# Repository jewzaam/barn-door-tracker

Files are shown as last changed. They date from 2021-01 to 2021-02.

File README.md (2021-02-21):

When taking pictures of the stars you will get star trails if you don't compensate for the earth's movement.  In some cases this may be a desired shot!  It can be a pretty cool picture.  But for deep sky imaging it's not desired.

I am just getting into astrophotography.  I know it can be expensive to buy gear and I don't know, well, anything yet.  To get started and start learning I made a couple prototype isosoles [barn door trackers](https://en.wikipedia.org/wiki/Barn_door_tracker), one mechanical and one motorized like this, to prove it works.  Then I decided to get more precise and 3D print things.

All docs are in `docs/` and there is an [Index](docs/00-index.md).  My goal is to write up everything you need in order to print, assemble, and use this tracker.  Hope you find some value in this!

Clear Skies!

## Tracker Explained

Posted an 8 min video giving an overview of my setup.

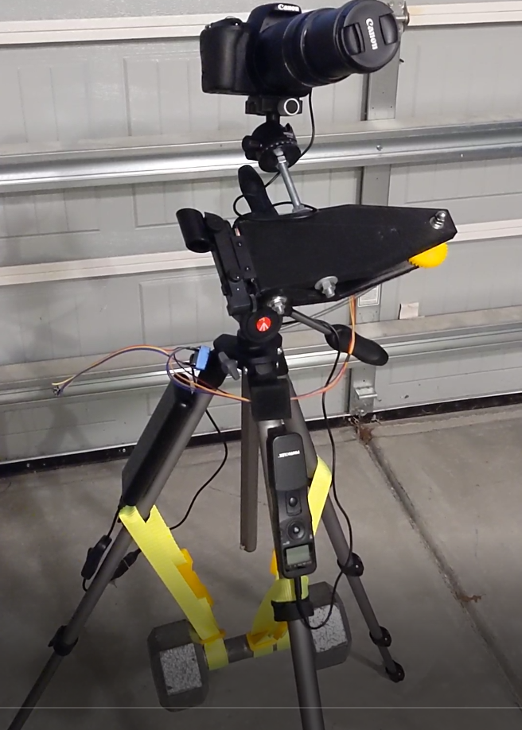
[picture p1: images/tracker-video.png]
Barn Door Tracker Overview (https://youtu.be/gP029RHcJ4Q)


## Tracker in Action
Tracker in Action
All setup and ready to go.  Battery on left leg, intervalometer on right, and 15 lb weight in the backpack.

## [Orion Nebula](https://www.astrobin.com/4iprt9/)<br>
M42
Canon EOS Rebel SL2, 300mm Lens, ISO1600<br>
866 x 5 second lights (1 hr 12 min 7 sec)<br>
[DeepSkyStacker](http://deepskystacker.free.fr/english/index.html) and [GIMP](https://www.gimp.org/).

## [Flame and Horsehead Nebulas](https://www.astrobin.com/a59dnw/)<br>
Flame and Horsehead Nebula
Canon EOS Rebel SL2, 300mm Lens, ISO3200<br>
621 x 5 second lights (50 min 50 sec)<br>
[DeepSkyStacker](http://deepskystacker.free.fr/english/index.html) and [Affinity Photo](https://affinity.serif.com/en-us/photo/).

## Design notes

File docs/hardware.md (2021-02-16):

# Hardware
I staretd out developing this for a Raspberry Pi 4b.  Since I have to the Raspberry Pi Pico for a couple of reasons:

* it's cheaper
* it's easier to smaller
* it starts almost instantly
* it doesn't get as hot

You can still find the older Raspberry Pi 4b [wiring](../imsages/../images/wiring-4b.png) and [software](../src/python/stepper.py), but it is not going to be kept up to date.  At some point I'll likely drop them since the MicroPython code is different enough.

## Raspberry Pi Pico

- File: [main.py](../src/microPython/main.py)
- Config: [stepper.yaml](../src/microPython/stepper.yaml)

The code doesn't hard wire pins but you do have to configure it.  See the [Calibration](#calibration) section on why you don't need to tune the stepper delay.

So just plug in your configuration in [stepper.yaml](../src/microPython/stepper.yaml) and ship the [microPython](../src/microPython/) directory to your Raspberry Pi Pico.

How?  I will leave that to you but provide the tools I used.  I decided to go the VSCode route which is GREAT!  I have one IDE to manage the code, run it remotely on the Pico, and finally to upload it to the Pico.  The sites I found helpful:

- [Raspberry Pi Pico: Getting Started](https://www.raspberrypi.org/documentation/pico/getting-started/)
- [How To Solder Pins to Your Raspberry Pi Pico](https://www.tomshardware.com/how-to/solder-pins-raspberry-pi-pico)
- [Developing for the Raspberry Pi Pico in VS Code — Getting Started](https://medium.com/all-geek-to-me/developing-for-the-raspberry-pi-pico-in-vs-code-getting-started-6dbb3da5ba97)
- [MicroPython libraries](https://docs.micropython.org/en/latest/library/index.html)

Once you get everything uploaded to the Pico it pretty much instantly starts when plugged into USB power.  The Raspberry Pi 4b I used originally took a while.  And it's cheaper, smaller, and MUCH cooler when running.

## Wiring

Pinout picked to minimize wire crossings.  It will change if I start adding some buttons.  Also I used [F-wire-blank.stl](../src/stl/F-wire-blank.stl) to make some blanks for pins not used so I could glue the wires together.  It was super annoying getting to a site to shoot and having to re-wire things!  Thankfully having this repo with pictures made it trivial, but still didn't like it.

The pinout is available on  [Raspberry Pi Pico: Getting Started](https://www.raspberrypi.org/documentation/pico/getting-started/):

Raspberry Pi Pico Pinout

And the layout I have gone with is:

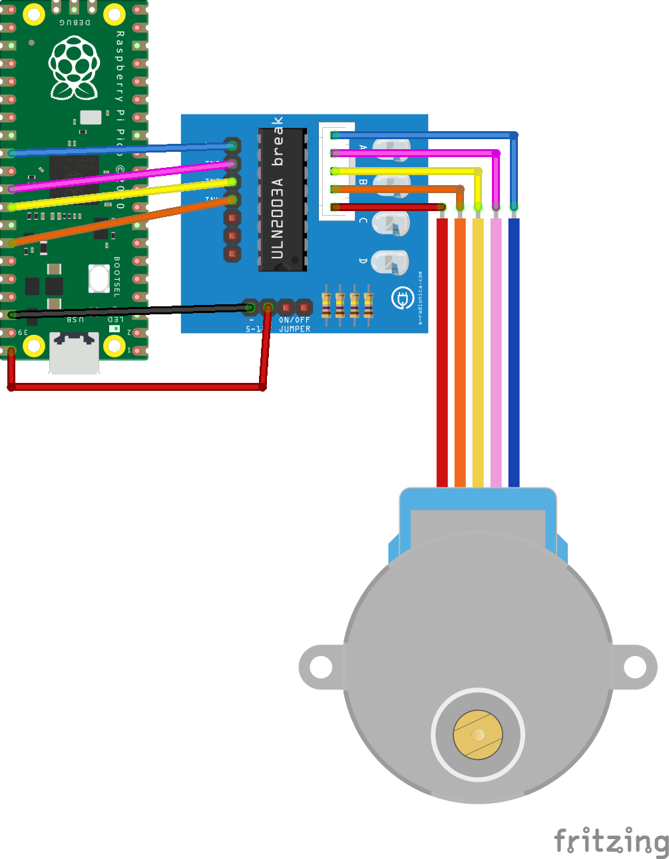
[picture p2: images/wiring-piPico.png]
Raspberry Pi Pico Wiring


## Controls

If you have wired up buttons or a switch (I use a [5-way navigation switch](https://www.adafruit.com/product/504)) you can control the speed of the stepper.  The wiring included is what I used with the switch above so I will talk about it in terms of the directions on that switch: up, down, left, down, and center (press).

When the tracker starts you can have it locked by default.  Control this in [stepper.json](../src/microPython/stepper.json) with `.start_locked`.

- hold control = toggle lock state, hold for `.controls.hold_lock_s` seconds
- up = if unlocked, turn on stepper (forward)
- down = if unlocked, stop stepper
- left = if unlocked, speed up stepper by `.controls.faster_increment`
- right - if unlocked, slow down stepper by `.controls.slower_increment`

Note that faster and slower increments are changes in the configured stepper radius `.tracker.radius`.  The names are not great, sorry.  When you tell this to go faster or slower it is just tweaking the radius and recalculating the step delay.  These values are not written to file.  I had problems getting that to consistently work.

The on-board Pico LED is used to indicate changes...

## Pico LED

The on-board Pico LED (gpio=25) is used to show state and status.

* solid on - tracker controls are unlocked
* solid off - tracker controls are locked
* blinking - various information

The LED blinks briefly when increasing or decreasing stepper speed.

The LED blinks in a pattern to indicate how much adjustment there is from the configured value.  This is shown when the stepper goes from **unlocked** to **locked**.  Initially, the LED turns off.  If the stepper is at the default state it immediately blinks 3 times.  If the stepper is faster it stays off for 2 seconds before blinking.  If the stepper is slower it stays off for 10 seconds before blinking.  If faster or slower, after the delay the LED blinks on once for each step above or below the default speed.  

So if you increased speed 5 times and lock controls the LED will:

1. turn off
2. wait 2 seconds
3. blink 5 times
4. turn off

---
Back to the [Index](00-index.md)!

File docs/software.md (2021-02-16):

# Hardware & Software

I staretd out developing this for a Raspberry Pi 4b.  The code is still there (see [stepper.py](../src/python/stepper.py)) but I have moved on to the Raspberry Pi Pico which is very different.  This document assumes:

- You are using a Raspberry Pi Pico
- You are wiring it the same way documented here
- You can change the code if you use another device or wire it differently

## Accuracy

The current software uses timers for:
* stepper control
* input (irq)
* blinking led

Therefore it is very accurate.  Tuning the radius of the tracker dynamically shows a higher error % on shutdown (print to stdout) but this is momentary in reality because of the use of timers.  Best case is turning on the Pico and no touching any controls until termination.  On termination you get the percentage drift between actual and expected times.  In a 60 second test I got this output:

```shell
avg_actual_delay_ms: 4.94393
total_error_p: -0.01140833%
```

After 4 minutes:

```shell
avg_actual_delay_ms: 4.943915
total_error_p: 0.04760027%
```

After 11 minutes:

```shell
avg_actual_delay_ms: 4.941289
total_error_p: 0.04693866%
```

- `avg_actual_delay_ms` is average delay in ms for each step
- `total_error_p` is the error between actual and expected total times

As you can see, it's pretty close.  It does accumulate some error but it isn't much.  And errors are momentary.  The timer will stive for the configured frequency regardless of what has happened on previous executions.

This is done by having the interupts (timer or irq) set a boolean flag and return.  There's a main control loop that then takes those flags to perform the actions required.  This way the timer blocks as little as possible.  Keep in mind the execution time for a periodic timer (used for stepper control, button input, and led blinking) callback is not part of the timer's period.  Setting 4 coil states took about 250ms.  Having that inside the timer results in a 250ms longer delay than expected.  By moving it out to the main control loop and not part of the timer's interuupt it is executed while the timer is waiting to fire again.

## How Hot Does it Get?

You might worry on a hot summer night about the temperatures.  I was wondering myself!  So I did a very simple test of the temperatures of the Pico, drive controller, and stepper in my office.  They were all resting on my bamboo desk.  The Pico powered by a USB battery (same one I take out for pictures).  The office ambient temperature is 74F.  I am rounding the temperatures as this is only to give peace of mind, not to be a rigerous study of how these components heat up over time.  And the times are simply when I remembered to take the temperatures, not premeditated!

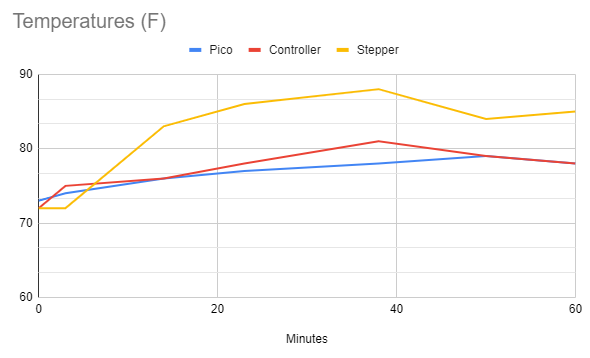
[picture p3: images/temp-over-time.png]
Temperatures over Time


---
Back to the [Index](00-index.md)!

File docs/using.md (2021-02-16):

# Using the Tracker

I am not going into details.  There's enough online on how to use these things.  The basic summary once everything is assembled, code installed, and electronics wired up:

1. Mount tracker on tripod with tracker closed, off, and gears engaged
2. Do polar alignment (use the visual sight if nothing else to get close)
3. Mount camera
4. Turn on tracker
5. Use camera (focus, test shots, exposures etc)

Note I turn on the tracker BEFORE using the camera.  This minimizes star trails from the beginning and makes staying on target easier.  Also, from what I am reading / hearing from folks at 200mm and a comercial low end tracker you'll get 20s to 30s shots.  What you can get depends greatly on polar alignment and correct configuration of the tracker.  Be prepared to try out a lot of things to dial it in!

It's doing its job if you can do a longer exposure with this than untracked.

When done for the night:

1. Turn off tracker
2. Unmount camera and take flats (in whichever order works for you)
4. Setup to take darks
5. While taking darks, take tracker off tripod and cleanup / stow gear

---
Back to the [Index](00-index.md)!

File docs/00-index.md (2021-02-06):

So it's not all in one massive file:

* [Background](background.md)
* [Pricing](pricing.md)
* [Building the Tracker](building.md)
* [Assembly](assembly.md)
* [Hardware](hardware.md)
* [Software](software.md)
* [Using the Tracker](using.md)

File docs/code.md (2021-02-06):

# Code

I staretd out developing this for a Raspberry Pi 4b.  The code is still there (see [stepper.py](../src/python/stepper.py)) but I have moved on to the Raspberry Pi Pico which is a little different.  This document assumes:

- You are using a Raspberry Pi Pico
- You are wiring it the same way documented here
- You can change the code if you use another device or wire it differently

# Raspberry Pi Pico

- File: [main.py](../src/microPython/main.py)
- Config: [stepper.yaml](../src/microPython/stepper.yaml)

The code doesn't hard wire pins but you do have to configure it.  See the [Calibration](#calibration) section on why you don't need to tune the stepper delay.

So just plug in your configuration in [stepper.yaml](../src/microPython/stepper.yaml) and ship the [microPython](../src/microPython/) directory to your Raspberry Pi Pico.

How?  I will leave that to you but provide the tools I used.  I decided to go the VSCode route which is GREAT!  I have one IDE to manage the code, run it remotely on the Pico, and finally to upload it to the Pico.  The sites I found helpful:

- [Raspberry Pi Pico: Getting Started](https://www.raspberrypi.org/documentation/pico/getting-started/)
- [How To Solder Pins to Your Raspberry Pi Pico](https://www.tomshardware.com/how-to/solder-pins-raspberry-pi-pico)
- [Developing for the Raspberry Pi Pico in VS Code — Getting Started](https://medium.com/all-geek-to-me/developing-for-the-raspberry-pi-pico-in-vs-code-getting-started-6dbb3da5ba97)
- [MicroPython libraries](https://docs.micropython.org/en/latest/library/index.html)

Once you get everything uploaded to the Pico it pretty much instantly starts when plugged into USB power.  The Raspberry Pi 4b I used originally took a while.  And it's cheaper, smaller, and MUCH cooler when running.

## Wiring

I chose this layout before physically using it.  It works but there is wire crossover which irks me.  The pinout is available on  [Raspberry Pi Pico: Getting Started](https://www.raspberrypi.org/documentation/pico/getting-started/):

Raspberry Pi Pico Pinout

And the layout I have gone with is:

Raspberry Pi Pico Wiring

## Calibration

You do not have to do calibartion!  This is done automatically.  This section just summarizes the techinque and what to look for in the debug output if interested in how close to expected values things are when you run the code.

This script is simple but not trivial.. it does a dynamic calibration of the delay between steps.  It measure actual time vs expected time and adjusts the delay between steps.  It's done the whole time the program runs.  The key is to do a pretty short sampling.  If you do a long sample it ends up oscillating, swingging wider over time from ideal.  The new step delay is also adjusted to be only 50% of the difference between what would have been ideal and what is currently set.  This simply means a slower change in the delay, again to tamp down on ocillations.  The way it is setup right now works very well to dial in to a reasonable margin of error and keep it there.

Note the error is higher on startup because it is based on the ideal data sheet numbers.  In my testing, _within 10 seconds_ the error rate stars hovering around `0.01%` with a few bips higher but overall very good.

## Custom Sleep

On the Pico I found the sleep functionality to be lacking.  Best I could get was about 1ms granularity.  That's not nearly good enough.  So I wrote a new function, _usleep_, that tries to hit a microsecond target.  It is a busy wait and it's pretty good.  A word of caution on the accuracy (second argument in the function).  If you change the value to be 100% (1.0) you'll be guarneteed to always have longer sleep times than you want.  Why?  Because if the slept time must 100% of the target we'll at best be EXACTLY right.  That never happens.  It will ALWAYS be slightly long.  With a 99% accuracy we allow a little slop and it all averages out pretty well since you'll end up both over andi under.  If you want to tune it I highly recommend you run the code and review the output when the program is terminated.

While on the exit info being printed.. do **NOT** run with `debug = True` when tracking!  This causes a huge load and results in wildly inaccurate sleep times.  Keep the code as lean as possible!

## How Hot Does it Get?

You might worry on a hot summer night about the temperatures.  I was wondering myself!  So I did a very simple test of the temperatures of the Pico, drive controller, and stepper in my office.  They were all resting on my bamboo desk.  The Pico powered by a USB battery (same one I take out for pictures).  The office ambient temperature is 74F.  I am rounding the temperatures as this is only to give peace of mind, not to be a rigerous study of how these components heat up over time.  And the times are simply when I remembered to take the temperatures, not premeditated!

Temperatures over Time
---
Back to the [Index](00-index.md)!

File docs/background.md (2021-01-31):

# Background

## Untracked
When taking pictures of the stars you will get star trails if you don't compensage for the earth's movement.  In some cases this may be a desired shot!  It can be a pretty cool picture.  But for deep sky imaging it's not desired.

For example, here's a 30 second exposure of M42 (Orion Nebula) taken with a 300mm lens.

M42 Untracked 30s

## Manual Tracker 
In order to get better shots of stars (astrophotography) I decided to build a barn door tracker.  My first version was an isometric version, meaning the threaded rod was straight and pivoted to keep in contact with the bottom board as it was rotated.  But it was also manual.  Humans are not good at spinning something consistently at such slow speeds without introducing additional vibrations!

Tracker v1

And it works!  Here's the same shot of M42 but for 150 seconds using the tracker.  It was processed a bit to make the nebula pop out more.  But the point is the lack of star trails.

M42 Manual Tracking 150s

You'll also notice that it isn't super clean.  And my experience doing this wasn't amazing.  Standing still for 2.5 minutes slowly cranking the tracker.. I got distracted, fell behind, added vibrations etc.

## Something Better...

I wanted to get a better shot and not have to manually manipulate this.  After a bit of research I settled on small stepper motor with controller driven by a Raspberry Pi I had laying around.  I have never used a stepper motor so it was a great excuse to learn even more new things.

---
Back to the [Index](00-index.md)!

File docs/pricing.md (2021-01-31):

# Pricing

You may be wondering how much all this will cost you.  I'm breaking down the hardware I used including the estimated plastic by weight from Cura based on my print settings.  For example, I used a small torch to heat the rod for bending on a custom built curved form.  I do include the cost of a Raspberry Pi Pico, though I have not built this with a Pico yet.  I will though so it's a valid cost!

I do **not** include:
- tools
- failed prints
- test prints
- electricity for 3D printer
- cost of items bought in packs larger than what was required
- tripod mounting hardware
- tracker power supply
- and other misc used to build the tracker

This cost is only of parts that end up on your tripod for imaging.

**Grand Total:** $56.08

In the cost breakdown here you can see the _camera mount_ is 53% of the cost.  It's worth it.

## Hardware Store

| Count | What | Cost Each | Total Cost |
| --- | --- | --- | --- |
| 2 | 608-ZZ Bearing | $0.69 | $1.39 |
| 5 | 1/4" Washer | $0.13 | $1.04 |
| 1 | 5/16" x 5" Hex Bolt | $0.64 | $0.64 |
| 1 | 5/16" Hex Nut | $0.13 | $0.13 |
| 1 | 3/8"-16 x 12" Threaded Rod | $1.52 |  $1.52 |
| 3 | 3/8"-16 Hex Nut | $0.14 | $0.42 |
| 2 | 3/8" Washer | $0.15 | $0.30 |
| 1 | 1/4"-20 x 24" Threaded Rod | $1.98 | $1.98 | 
| 3 | 1/4" Hex Nut | $0.08 | $0.24 |
| 2 | 1/4" Lock Washer | $0.19 | $0.38 |
| 2 | 1/4"-20 Cap Nut | $0.25 | $0.49 |
| 2 | #8-32 Bolt | $0.12 | $0.24 |
| 2 | #8 Nut | $0.10 | $0.20 |
| 2 | #8 Washer | $0.08 | $0.16 |
| 2 | M4-0.7 x 8mm Set Screw | $0.37 | $0.74 |

## 3D Prints

Printed parts I calculate based on $23.00 / 1 kg for filament and the settings noted in [Building: Print Settings](building.md#print-settings).

| What | Filament | Cost |
| --- | --- | --- |
| Stepper Gear | 3g | $0.07 |
| Threaded Rod Gear | 17g | $0.39 |
| Tracker Top | 168g | $3.86 |
| Tracker Bottom | 147g | $3.38 |
| Raspberry Pi Pico Case | 6g | $0.14 | 
| ULN2003 Case | 18g | $0.41 |

## Electronics and Camera Mount

And finally other parts.  This includes the camera mount, which is by far the most expensive part.  You don't want your camera to slip though, so it's worth finding something reasonably good.

| What | Cost |
| --- | --- |
| 28BYJ-48 + ULN2003 | $2.48
| Raspberry Pi Pico | $5.00 |
| 6 x F/F Jumper Wire | $0.49 |
| [Tripod Head](https://amazon.com/gp/product/B08FB2Q5RC/) | $29.99 |

---
Back to the [Index](00-index.md)!

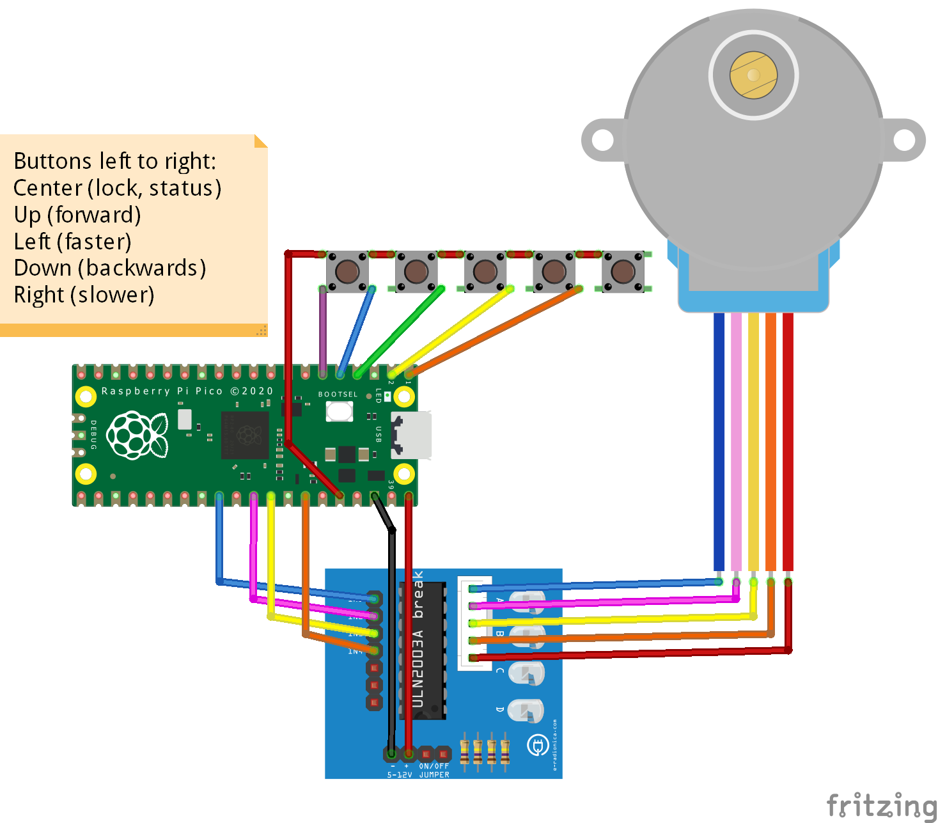
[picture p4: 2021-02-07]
images/piPico+uln2003+28byj-48+5waySwitch.png

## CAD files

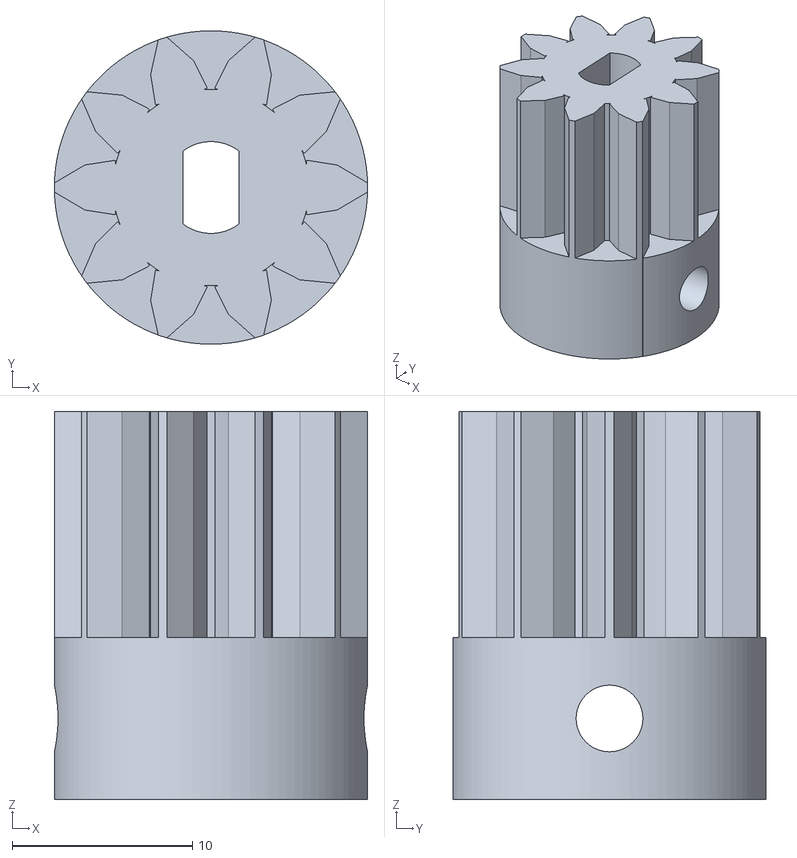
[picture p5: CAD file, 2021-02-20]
src/stl/GEAR-stepper.stl
17.4 x 17.4 x 21.5

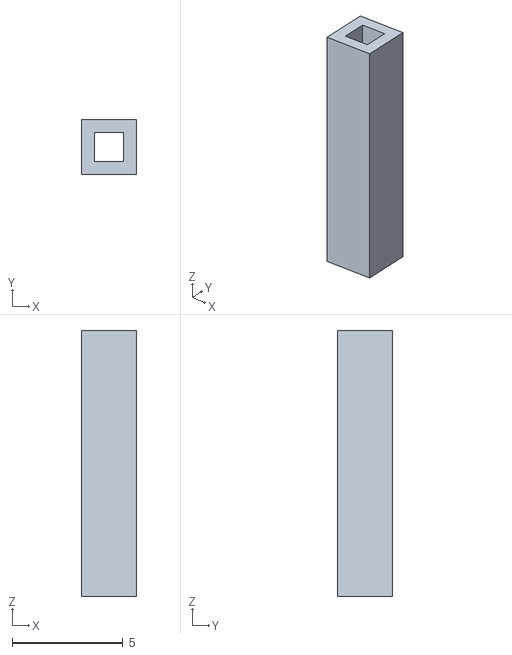
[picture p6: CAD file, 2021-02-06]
src/stl/F-wire-blank.stl
2.50 x 2.50 x 12.0

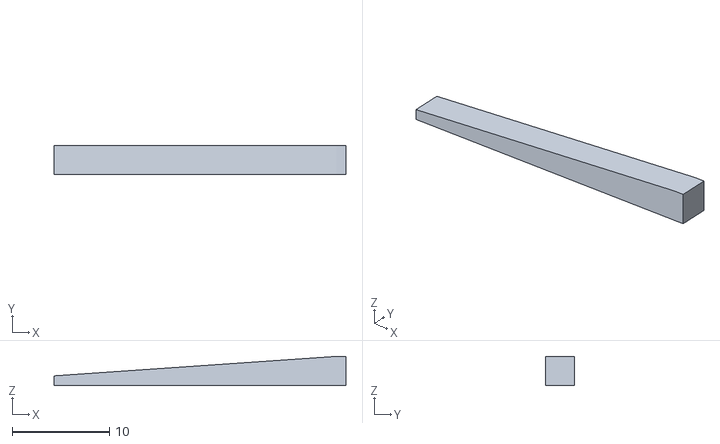
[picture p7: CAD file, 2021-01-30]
src/stl/mini-wedge.stl
30.0 x 3.00 x 3.00

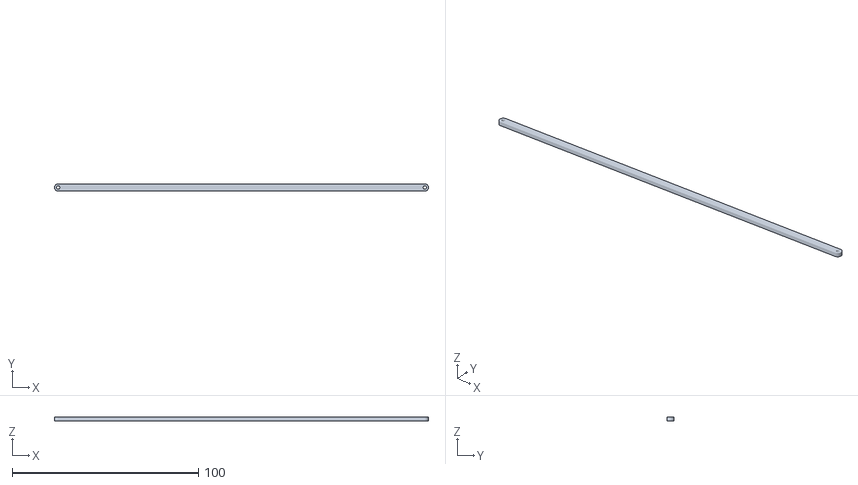
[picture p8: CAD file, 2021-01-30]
src/stl/HELPER-compass.stl
200.8 x 4.00 x 2.00

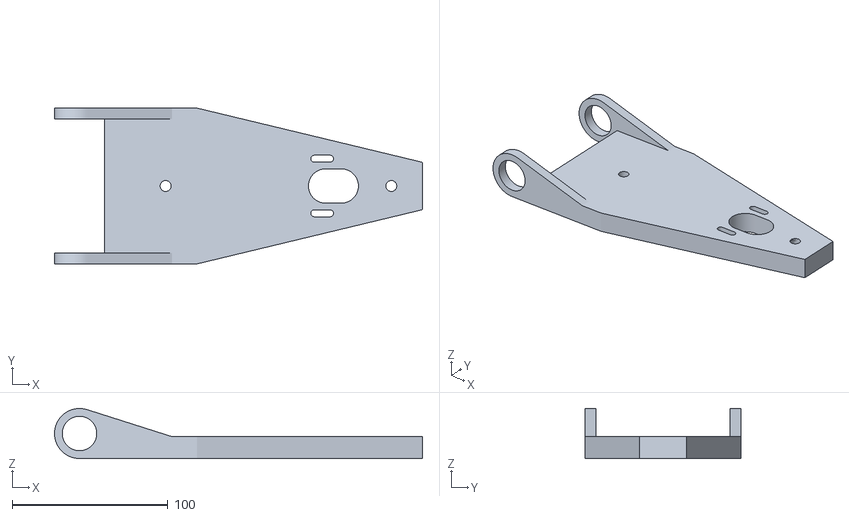
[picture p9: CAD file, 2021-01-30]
src/stl/tracker-bottom.stl
236.1 x 100.0 x 32.1

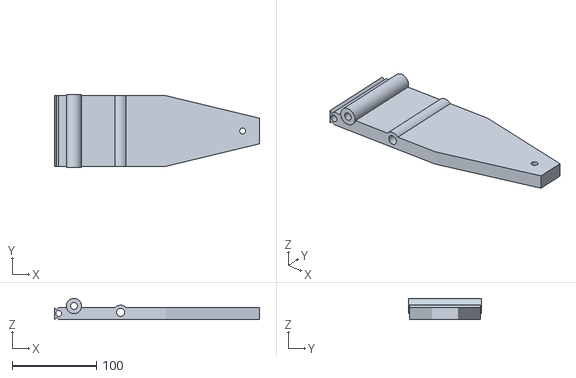
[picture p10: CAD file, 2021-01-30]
src/stl/tracker-top.stl
243.1 x 86.0 x 25.1

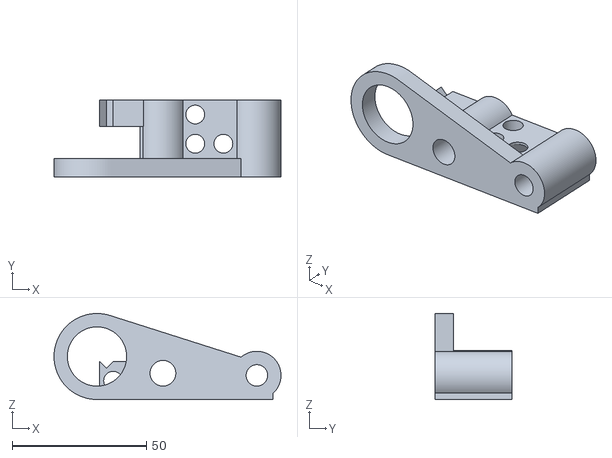
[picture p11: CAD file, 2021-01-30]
src/stl/TEST-hardware.stl
84.7 x 28.8 x 32.1

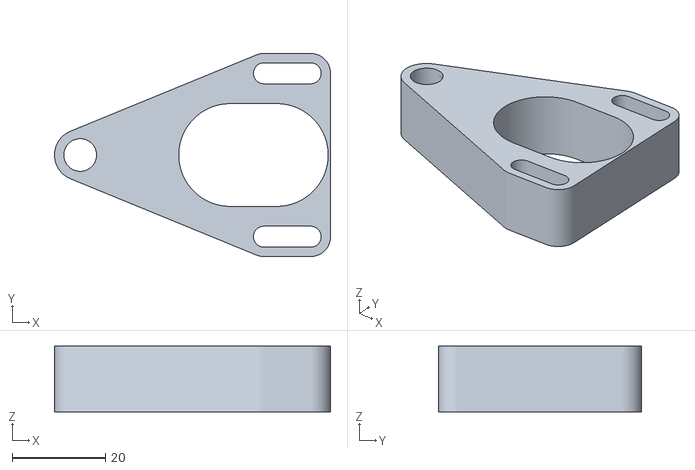
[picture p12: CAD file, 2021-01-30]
src/stl/TEST-gears.stl
59.1 x 43.5 x 14.0

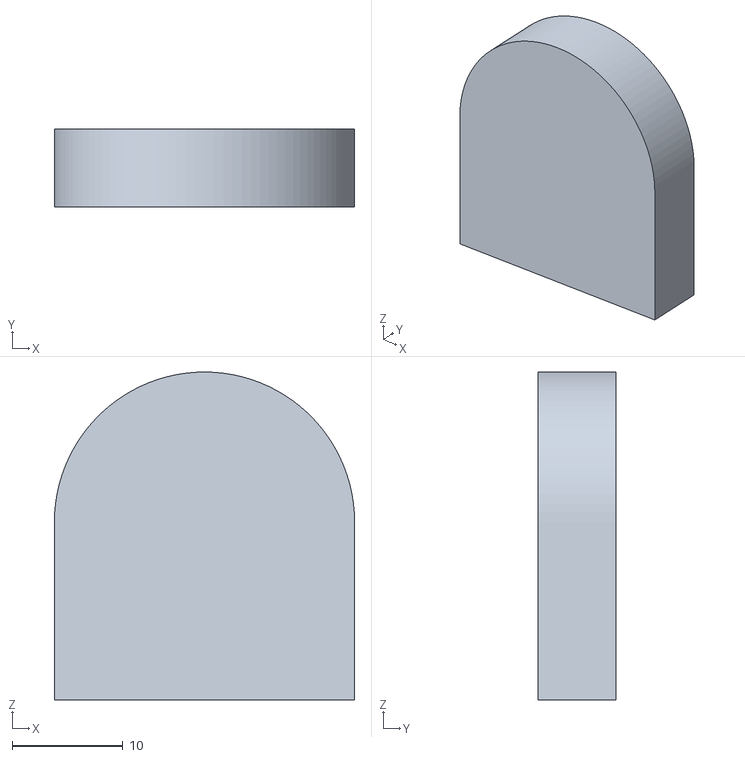
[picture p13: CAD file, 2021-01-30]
src/stl/support-bearing.stl
27.1 x 7.00 x 29.6

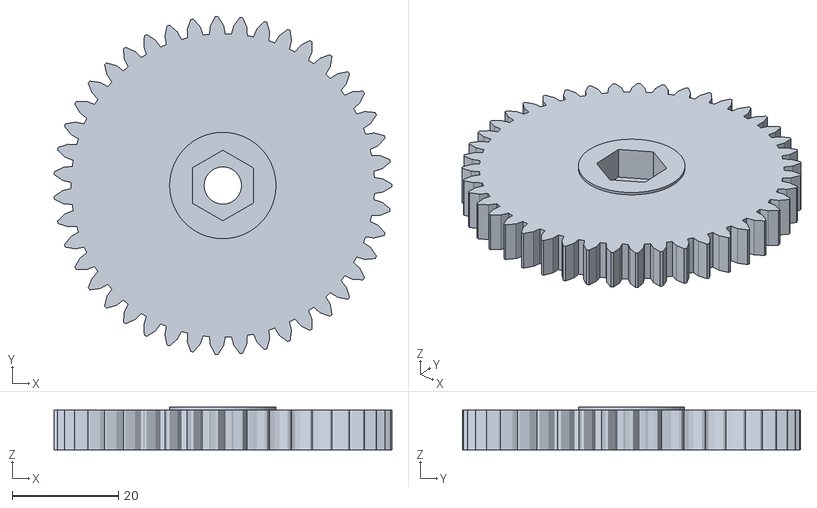
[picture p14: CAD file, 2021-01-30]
src/stl/GEAR-rod.stl
63.6 x 63.6 x 8.00

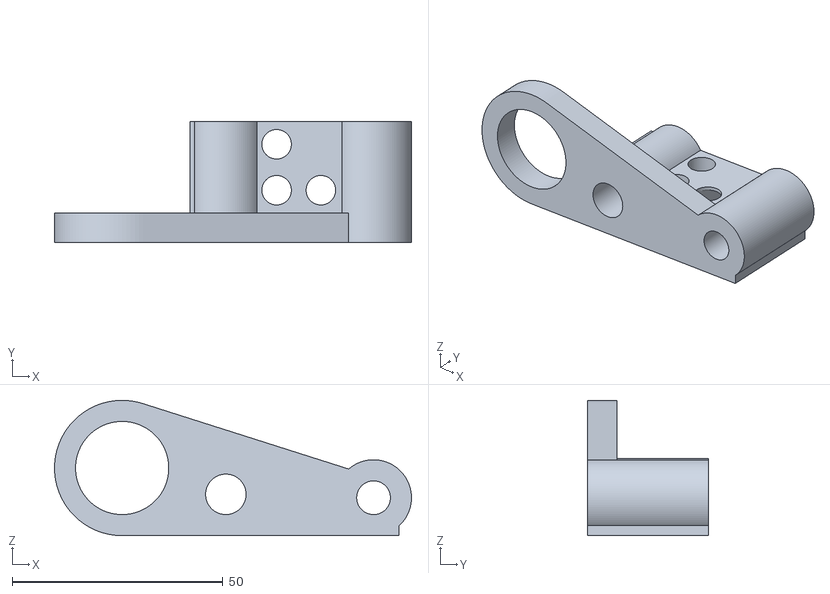
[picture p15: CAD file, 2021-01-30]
src/stl/TESTER-hardware.stl
84.7 x 28.8 x 32.1

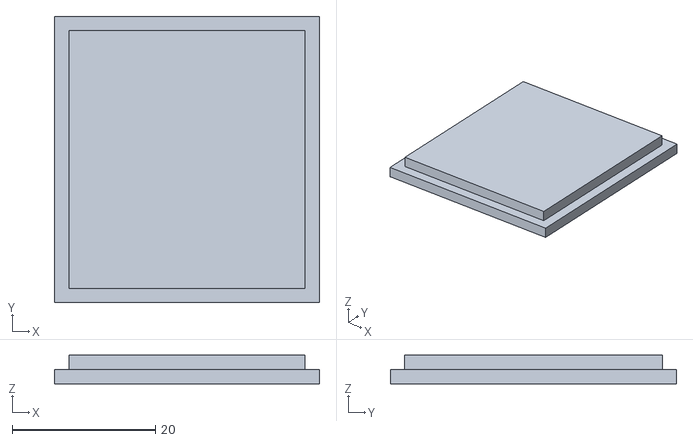
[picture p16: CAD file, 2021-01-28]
src/stl/ULN2003-lid.stl
37.0 x 40.0 x 4.00

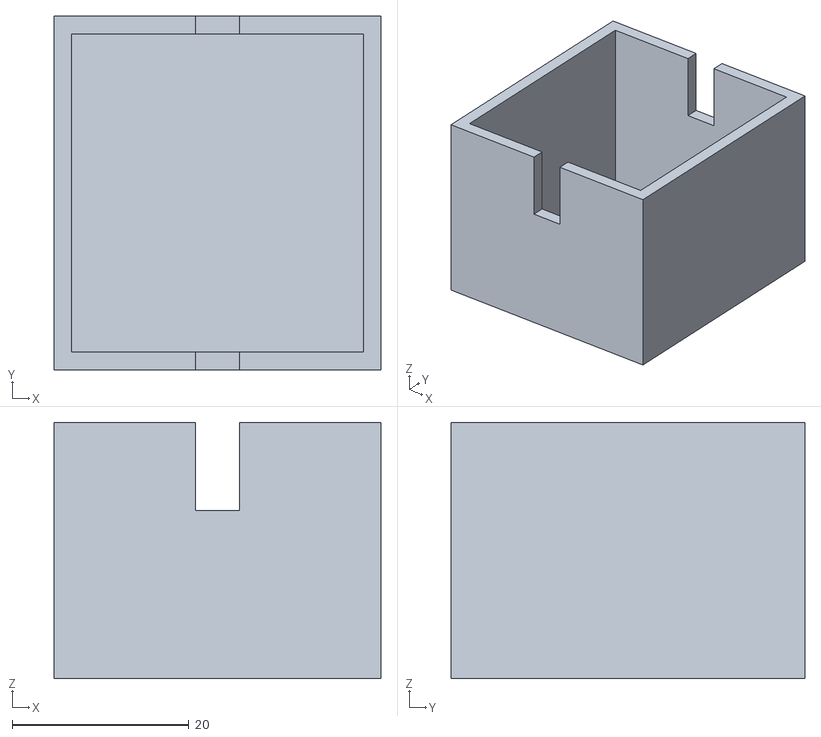
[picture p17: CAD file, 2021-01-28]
src/stl/ULN2003-case.stl
37.0 x 40.0 x 29.0

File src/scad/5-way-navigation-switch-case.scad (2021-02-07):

// quick case and button for 5-way navigation switch
// https://www.adafruit.com/product/504
// adafruit product id 504


switch_hole_d=5.9;


switch_base_xyz=[10.5,10.5,3.7];

case_body_d=20;
case_hole_d=9;
case_body_h=80;

thickness=2;

$fn=200;

/*

Create a case that can be held in hand for use.  The body of the case is a cylinder.  It has a ledge for the switch to sit on and a hole big enough for wiring to fit through.  A lit fits over the switch once it's resting on the ledge
*/

difference()
{
    cylinder(d=case_body_d,h=case_body_h,center=true);
    
cube([switch_base_xyz[0],switch_base_xyz[1],case_body_h+10],center=true);    
}

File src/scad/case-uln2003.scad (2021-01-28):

box_thickness=2;

box_hole_width=5;

box_hole_depth=10;

box_inner_dim=[33,36,25];

/* [Hidden] */

$fn = 300;


module lid()
{
    // lid
    union()
    {
        cube([box_inner_dim[0]+box_thickness*2,box_inner_dim[1]+box_thickness*2,box_thickness]);

        translate([box_thickness,box_thickness,0])
        cube([box_inner_dim[0],box_inner_dim[1],box_thickness*2]);
    }
}

// box
module box()
{
    difference()
    {
        // main body
        cube(box_inner_dim+[box_thickness*2,box_thickness*2,box_thickness*2]);

        // cut inside
        translate([box_thickness,box_thickness,box_thickness])
        cube(box_inner_dim+[0,0,box_thickness*2]);
        
        // cut slot for wires
        translate([box_thickness+box_inner_dim[0]/2-box_hole_width/2,-box_thickness,box_thickness*2+box_inner_dim[2]-box_hole_depth])
        cube([box_hole_width,box_inner_dim[1]+box_thickness*4,box_hole_depth+box_thickness]);
    }
    
}

lid();

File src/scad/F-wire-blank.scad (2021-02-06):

xyz=[2.5,2.5,12];
thickness=0.6;

difference()
{
    cube(xyz,center=true);
    cube(xyz+[-thickness*2,-thickness*2,thickness*2],center=true);
}

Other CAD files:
src/stl/gear-10.stl
src/scad/mini-wedge.scad
src/scad/tracker.scad

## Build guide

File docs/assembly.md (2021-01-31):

# Assembly

Follow the sub-sections in order...

## Prep: Sanding / Filing

1. Make sure the bottom plate is smooth where the 43 tooth gear will rest.
1. Make sure the bottom plate's rod hole is smooth but don't make it too wide!
1. Cleanup the bottom plate bearing support.  Don't get it so the bearing can be hand pressed in, you can do that with the bolt and a few larger washers.  Cleanup both sides EVENLY if possible!
1. Cleanup teeth on all gears.  Do not take off much material but make sure there are no odd protrusions that will cause gears to push each other and move the tracker.
1. Cleanup the inside of the stepper gear so it fits on the stepper motor.
1. Generally cleanup anything else.. 

## Bearings

Gently press the bearings into the bottom plate.  Be sure to put the pressure on the outer bearing race, not the inner, else you may damage the bearing.  It shouldn't be too hard to press it in, so if it's really hard cleanup some with a file or sandpaper.

To press them in stach washers such that the biggest washer is on the outer race and the hinge bolt won't slip through it.  Use washers on both sides.  Gently screw the bolt onto the bearing with the nut you have for the hinge.  

Remove bolt and repeat for the other bearing.

Here are some example pictures of me testing this process on the hardware test print.  Note this doesn't have the simple finder test print.  Flip the bolt around the other direction if that bumps into the bolt.

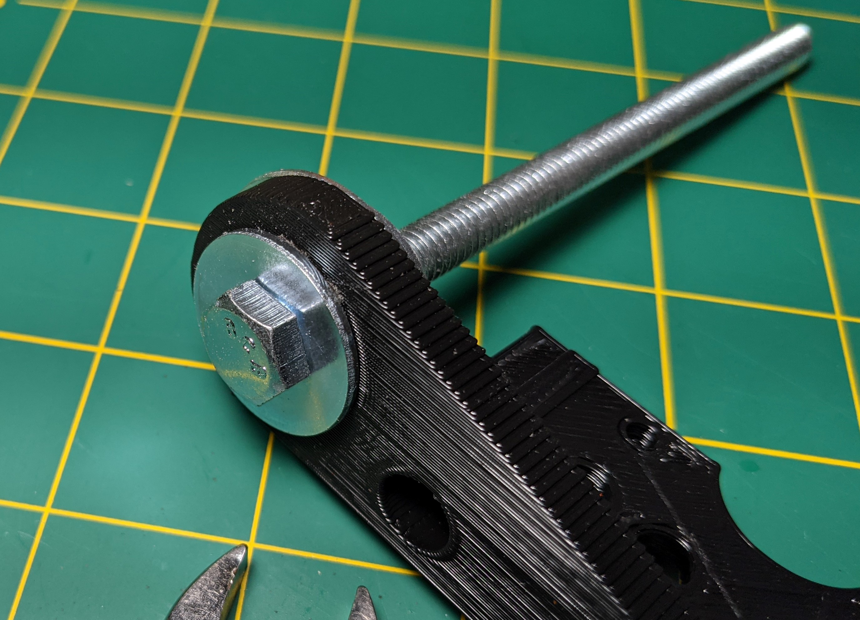
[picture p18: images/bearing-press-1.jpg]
Bearing Press 1

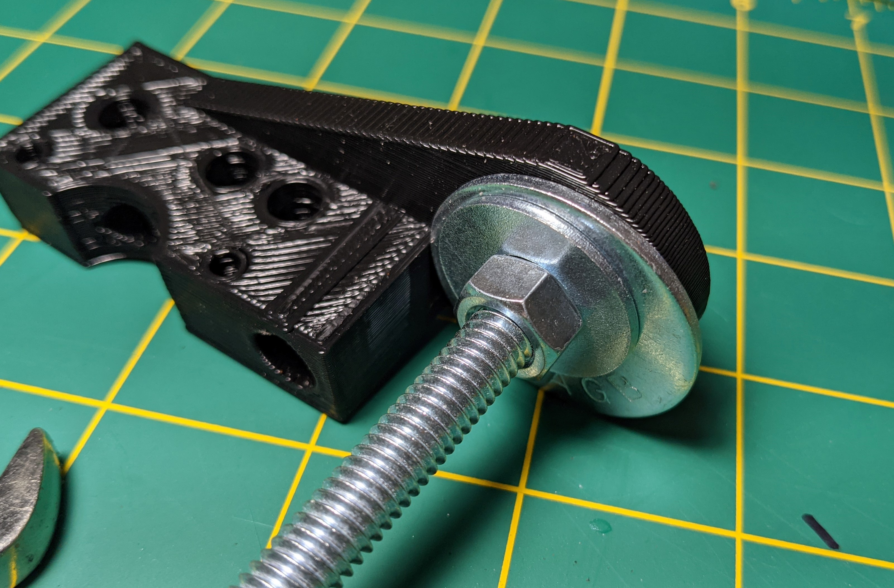
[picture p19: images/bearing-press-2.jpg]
Bearing Press 2

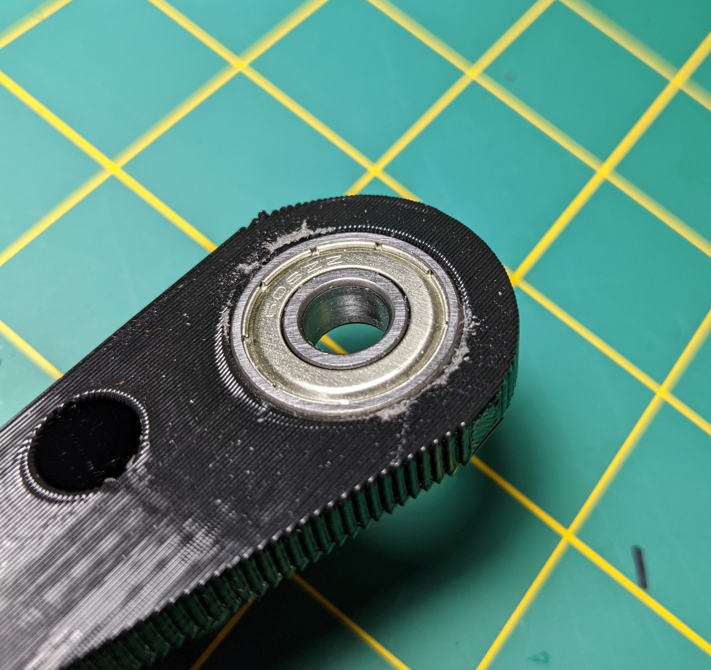
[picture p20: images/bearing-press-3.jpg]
Bearing Press 3


## Hinge Bolt

Make sure you get the right orientation for the plates.  When closed, the sides that were on your print bed are on the outside!

Note I am adding some 1/4" washers to ensure the bolt and nut have a solid and flat surface on the outside of the bearing.  This is not required.

Then...
1. Place the top plate in between the bearings in the correct orientation. 
1. Place one 1/4" washer on the 5/16" hex head bolt.
1. Thread 5/16" hex head bolt through one bearing.
1. Push or thread bolt through the top plate.
1. Add one 1/4" washer on the bolt.
1. Gently tighten.  This may mean tightening the bolt head if threaded through the top plate AND tightening the 5/16" nut.
1. Check alignment of the threaded rod holes between top and bottom.

### Troubleshoot

If the rod holes do not align it's probably due to over extrusion and filing away material inconsistently between the two bearing holes.  Mine was off by at least 1mm resulting in a huge misalignment at the end of the tracker.

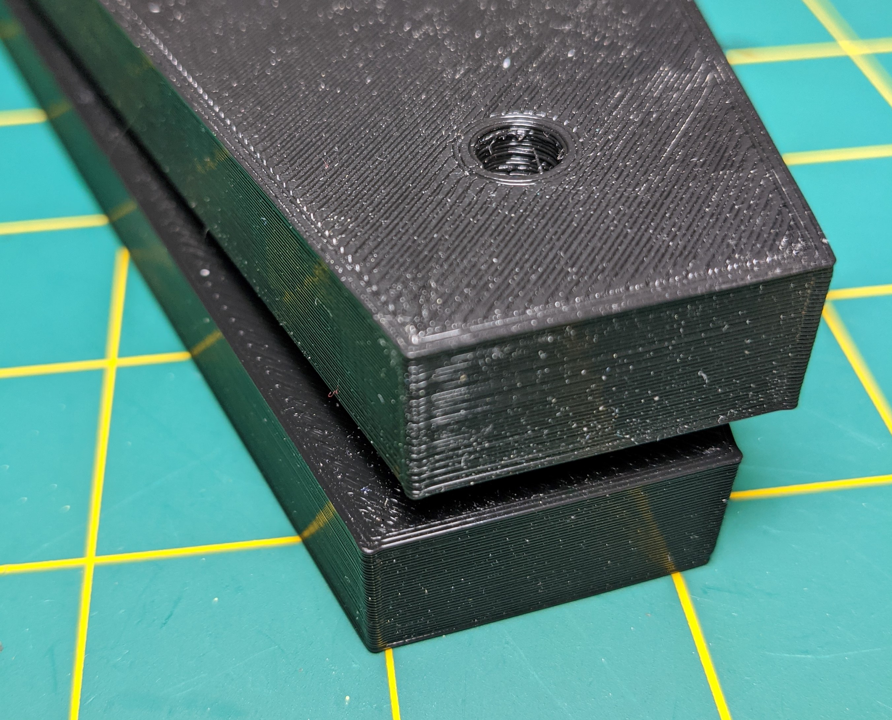
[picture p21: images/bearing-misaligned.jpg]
Bearing Misaligned


I don't know what I did wrong but whatever.  Going to make it work!  My solution was to find which hole needed adjustment and slowly sanding with 80 grit sandpaper on a dowel.  The side effect of this was a gap on the back side of one bearing.

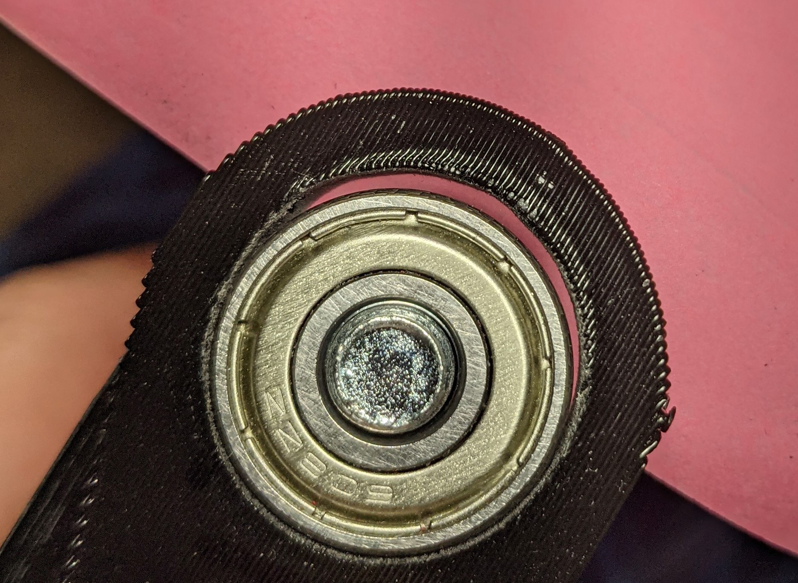
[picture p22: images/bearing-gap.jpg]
Bearing Gap


Create and print the [mini-wedge.stl](../src/stl/mini-wedge.stl) and if needed adjust with the [mini-wedge.scad](../src/scad/mini-wedge.scad).  Put in wedges as needed, glue in, and cut flush.  Do this after sanding and with your straight (not yet curved I assume) threaded rod inserted into both the top and bottom plates.  The closer you get this to perfect the better!  Which is why I'm bummed I had to write this section.  But it is what it is!

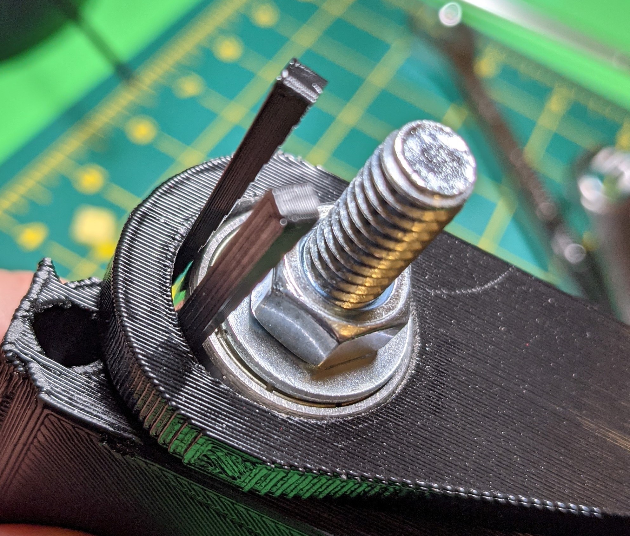
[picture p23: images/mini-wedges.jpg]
Mini Wedges


## Stepper Gear

You may have to push the 10 tooth gear onto the stepper motor.  But if you have to push really hard STOP.  Take the time to file down the inside.  You'll need some small hobby files, but if you have a 3D printer you should get some anyway.  Once it fits down snug but not too snug thread the #6 set screw into one side of the gear.  Optionally use a second #6 set screw.

**NOTE** take care to note if the stepper gear is tilted.  This is easier to do powered, since you can simply eyeball a full rotation and see if it seems the teeth wobble over the course of a rotation.

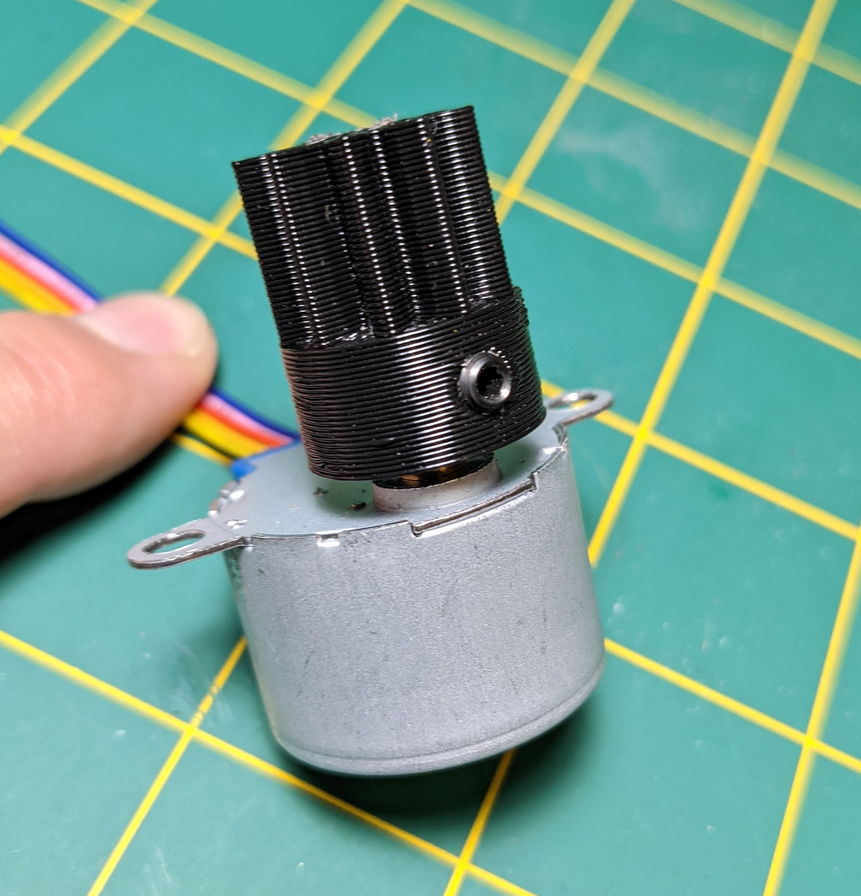
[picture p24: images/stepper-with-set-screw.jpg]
Stepper and Gear with Set Screw


## Stepper (with Gear)

Thread 2 #8-32 x 1" machine screws through the motor mounts into the 2 holes on the bottom plate.  Of course the gear must go UP into the bottom plate, so you can't get the orientation wrong unless you try really **really** hard..

Slide stepper as close to hinge as possible and **loosely** tighten bolts with #8-32 nuts, optional washers.  We will adjust the stepper location in a later step, but it's much easier to install before the threaded rod is on the tracker.

## Threaded Rod and Gear

For now just a quick summary.  More info to come..
1. Bend the rod.
1. Open tracker.
1. Secure to top with washers, lock washers, and nuts (1 ea top and bottom).
1. Install 43 tooth gear (with nuts).
1. Thread end of curved rod into bottom plate.
1. If necessary, bend AT THE TOP PLATE to get it to fit in the bottom plate.  Do not remove any curve!
1. Thread 1/4" cap nut on end of the curved rod.

**NOTE** Once you install this on a tripod you may find it is too long, interfering with tripod legs.  You'll get hours of time out of this even shortening it a lot.  Feel free to cut short with a hack saw, smooth out the threads, and put the nut cap back on.

## Adjust Stepper

With the threaded rod gear near the end of the curved rod..

Loosen the stepper bolts and slide it so that the stepper gear is interacting with the threaded rod gear where you want.  This may take some tuning to make sure it's not too loose or tight a fit.

**NOTE** imperfections in the gears may cause things to move around while taking shots.  If you notice things binding see if you can smooth any of the gears or adjust the distance between the stepper and threaded rod gears.

## Camera Bolt

Thread or push your 3/8" bolt through the camera bolt hole.  Tighten as needed.  Attach camera mount on the polar said of the tracker.

If this bolt is very long the whole thing will bounce more.  Using a 3/8" threaded rod for this allows you to adjust the length by changing how long the rod is on the camera (polar) side.

1. install one washer and nut
2. insert rod into camera hole
3. install other washer and nut
4. adjust location based on where you think you want the camera mount
5. tighten
6. thread one more nut
7. install camera mount
8. lock camera mount by tightening last nut on the base of the camera mount

Be careful not to tighten the nut too much on the camera mount.  Unless you got a really nice one (you didn't did you..) you could break the threads off of the mount.

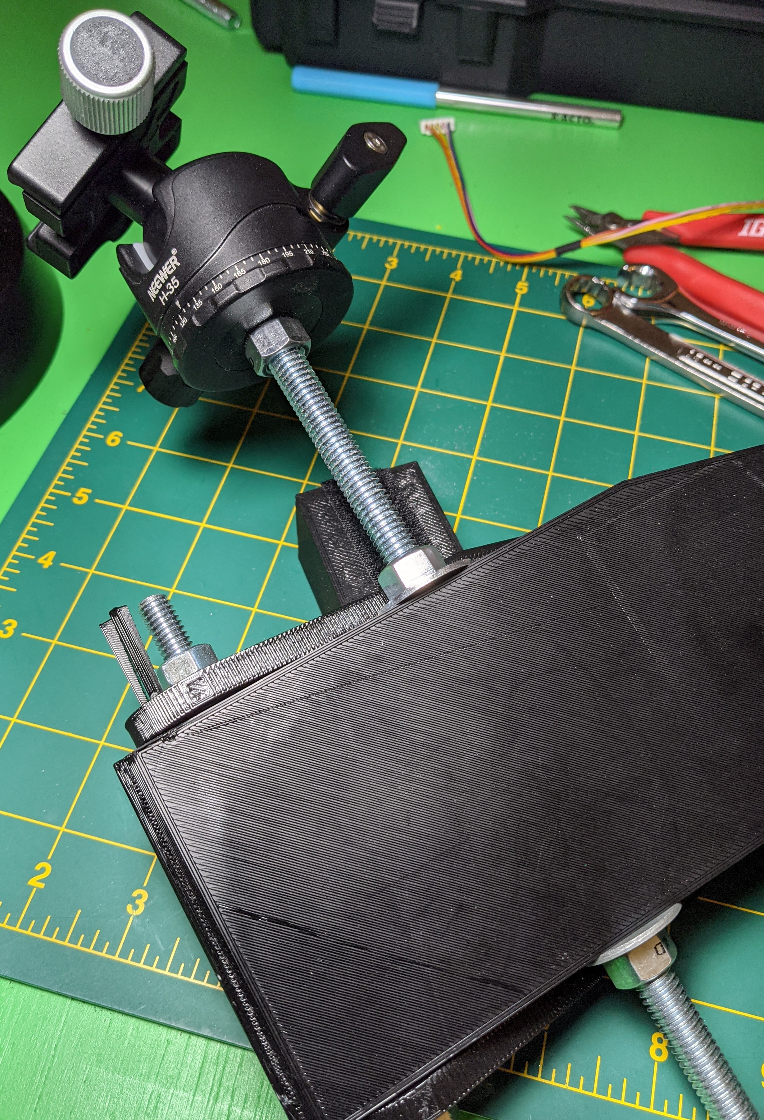
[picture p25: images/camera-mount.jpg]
Camera Mount


## Tripod Bolt

This is specific to your tripod.  You may need to replace the bolt you have on the tripod with something longer.  Whatever you have, thread it through the bottom plate hole and secure with a nut.  Consider a T-nut and a shorter bolt if you don't want it protruding.  The T-nut requires a wider hole and could be pressed in after heating (so the tines will melt the plastic when being pushed).

Note my bolt is too long and I plan to cut it short and heat a T-nut to secure it.  Just do what is right for your setup..

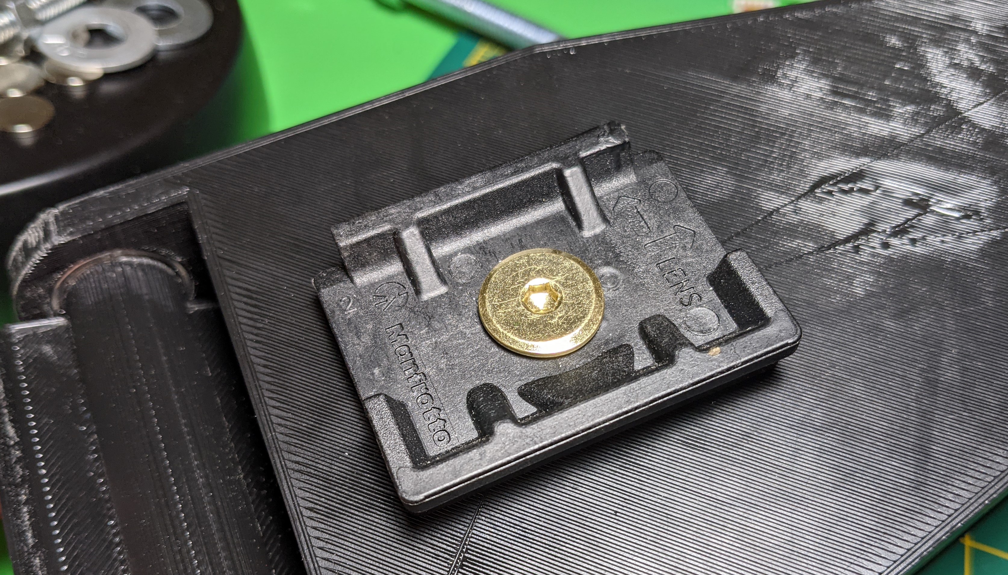
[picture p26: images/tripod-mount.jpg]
Tripod Mount


## Other Electronics

The drive controller and Raspberry Pi installation I leave to you.  Just make sure:
1. lights on these will not interfer with your pictures
1. the threaded rod will not hit them
1. they are in a good location when the tracker is both fully closed AND fully open

---
Back to the [Index](00-index.md)!

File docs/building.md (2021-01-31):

# Building the Tracker

NOTE I am not affiliated with Amazon.  Any links I provide are just to help you out by providing exmaple hardware!

## How does it work?

The first thing is to understand how the stepper works.  Actually, the first thing is to decide what stepper to use.  I selected the 28BYJ-48 stepper motor with ULN2003 driver board.  Once the parts arrived I dove in trying to understand how it works.

There are tutorials and data sheets. And they are almost right.  But they ultimately don't quite get you there.  Here are a few I was referencing:

* [28BYJ-48 Data Sheet](https://components101.com/motors/28byj-48-stepper-motor)
* [Raspberry Pi Stepper Motor Control with L293D / ULN2003A](https://tutorials-raspberrypi.com/how-to-control-a-stepper-motor-with-raspberry-pi-and-l293d-uln2003a/)
* [Adafruit's Raspberry Pi Lesson 10. Stepper Motors](https://learn.adafruit.com/adafruits-raspberry-pi-lesson-10-stepper-motors/overview)

What these give you is parts of the info but not everything.  And for reasons I cannot fathom the Raspberry Pi tutorial does not plug the stepper straight into the drive board!  I tinkered around and firgured out how to do it and here's the key things I learned.  Please keep in mind I haven't touched a Raspberry Pi since I setup OctoPi for my 3D printer 5 years ago, so I know almost literally nothing..

This model of stepper motor has 5 wires.  The colors are important, NOT the order they may be in the wiring harness.  Red is power, the others correspond to a coil by color.  There are 4 coils.  To move the motor you turn the coils on in a specific pattern.  There are several possible patterns but the recommended pattern uses 1/2 steps for this stepper.  Do that.  It's more steps in a sequence but you're writing code.  If it's just slightly more complex and RECOMMENDED who cares?

The wires from the stepper are connected on the side of the driver board with a clip for the stepper.  On the other side you hook up GPIO from the Pi.  The GPIO will will turn the coil ON.  This is important to note, as the data sheet indicates the sequence by which coil is held to ground and is therefore on.  So "0" on the data sheet is "1" in your program.

And don't forget power!  You can turn on the coil GPIO all you want, but without power turned on it does nothing.  Well, it still may do nothing if you wire it wrong, but that's a different problem!

Finally the question of speed.  This is controlled only by the delay between steps.  There's a HUGE gotya on this one:  each step will take a different amount of time.  Meaning it is not an accurate system.  But we can compensate for that.

Now for some math.  We are driving some gears that push a threaded rod.  We need to know how fast that rod will move.  The stepper has a motor in it and the data sheet gives how many degrees it moves per step. BUT it also has a gear reduction inside the motor.  So the stepper shaft moves on rotation based on that reduction.  The 28BYJ-48 stride angle is listed as "5.625°/64".  This means each step is 5.625° and the gear reduction is 64:1.  So one rotation is (360/5.625*64) = 4096 steps (using the recommended half step sequence).  This means to get our gears to turn at a specific rate we can simply put the right delay between steps.  But not really.  As noted, it isn't accurate.

To compensate for timing inacuraces in either the Pi or in the stepper I spent a good bit of time trying out things.  It's very easy to get a system setup that oscillates and gets worse over time.  The best pattern I found was to do a short snapshot of the expected vs actual time observed over a known number of steps and adjust the delay based on what was observed.  It won't be 100% accurate but we're talking 100's of ms over the course of half an hour, something like 0.025% drift.  Unless you're taking 30 minute exposures you won't notice it!  By the way, you won't take 30 minute exposures.  At 300mm I probably will try only 30 seconds. But that's better than the 2 seconds untracked by a LOT!

We have a stepper, and it's pretty accurate.  We just need to know what gears we're turning and the rod it's pushing so we know the delay for the stepper and the distance to put the rod from the pivot.  This model will let you pick these values if you have something different to work with.  

Key values to know:
* how many threads per mm for your rod
* how far center of rod is from the pivot point

I went with things from other models I saw around the interwebs and what I could get in my local hardware store:

* 1/4 inch threaded rod, 20 threads per inch
* rod 200mm from the hinge, because of print bed size

The radius (r) is 200mm.. And there are 0.7874 threads per mm (aka 20 threads per inch).  The circumference of the circle your rod travels is 2πr = 400π = 1256.6370mm.

The earth roughly rotates 360° / 24 hours, or 0.25° / minute.  Put another way, every minute the earth rotates 1 / 1440 % of the circumference of your circle.  That means every minute the rod needs to travel 0.8726mm.  (**NOTE** it isn't exactly / 24 hours, we will use the real value in the stepper code)

What we really need is the how many revolutions a nut on the rod must turn per minute.  Why the nut?  Our gear drives a nut, and one rotation is the distance of one thread along the rod.  And we pick one minute simply as a reasonable time scale to work with.  The rotation speed must be enough to move the rod 0.8726mm a minute.  Given 0.7874mm per thread that works out to 1.1082 rotations in a minute.

Now let's put that all together.  Our input date is:
- rod has 20 threads per inch (20 thread / 24.5 mm)
- radius of circle is 200 mm

Therefore we calculate the rotation required of the nut on the threaded rod per minute is:

(400π/1440) / (20/25.4) = 1.1082 revolutions per minute

Many barn door trackers work on a 1/4" rod at 290mm radius, which works out to 1 rotation per minute.  My motorized prototype did this just fine and the stepper could go faster.  This is a very doable number!  Let's get into building...

## Parts

Ok, explainations..

The tracker opens slowly on a hinge.  It's driven by your gears moving the threaded rod.  There are bearings at the hinge to help it be very smooth and the bolt just holds the bearings in the right place.  You attach the tracker to a tripod.  This should be sturdy.  Many tripods in the US have 3/8" bolts.  Mine has a 1/4" bolt.  You attach the camera on a separate camera mount.  I recommend a ball mount as the adjustment screws will not get in the way.  Again, in the US it's either 3/8" or 1/4".  Use the biggest you can for stability!

A note on camera mounting.  This model mounts it on the side of the tracker.  This provides more flexibility for getting shots.  If you mount it on the top it's likely you'll be limited since the ball mount won't allow enough movement to point at zenith.  I don't provide an option for a top mount because of this limitation.

If you are not using a 28BYJ-48 stepper motor you'll need ot adjust other parameters.  I won't get into these here.  And they're likely to be hard coded in the initial model anyway.  Sorry about that!

Buy the hardware first so you can measure things!

Make sure your hinge bolt is long enough.  You want the tracker to be around 4 inches (~100mm) wide.  If it's too long it's easy to cut it shorter with a hack saw.  It's really hard to make it longer..

If you don't have mini files yet do yourself a favor and get some.  They make cleanup much easier.  And if you get a set without handles just print some and heat press the file into the plastic!  I have a set similar to this [carbon steel 6 piece-set](https://amazon.com/dp/B07KH8BG1F/).

Hardware I used that is default for the model:
- Hinge
  - 2 ea: 608-ZZ bearings
  - 1 ea: 5/16" x 5" hex full thread bolt
  - 2 ea: 1/4" washer
  - 1 ea: 5/16" nut
- Camera Mount
  - 1 ea: 3/8" threaded rod
  - 2 ea: 3/8" washer
  - 3 ea: 3/8" nut
  - 1 ea: ball head tripod mount
- Threaded Rod
  - 1 ea: 1/4"-20 x 20" threaded rod (20 thread / inch)
  - 2 ea: 1/4"-20 nut
  - 2 ea: 1/4" washer
  - 1 ea: 1/4" washer (optional, under gear
  - 2 ea: 1/4" lock washer (optional)
  - 2 ea: 1/4"-20 cap nut (optional)
- Threaded Rod Gear
  - 1 ea: 1/4"-20 nut
- Stepper
  - 2 ea: #8 x 1" bolt
  - 2 ea: #8 washer
  - 2 ea: #8 nut
  - 1 ea: 28BYJ-48 stepper motor
  - 1 ea: ULN2003 driver board
  - 1 ea: Raspberry Pi of your choice
  - 6 ea: F/F jumper wire
  - 1 ea: 5V power supply for Raspberry Pi
- Stepper Gear
  - 1 ea: M4-0.7 x 8mm set screw

3D printed part list:
- 1 ea: 10 tooth stepper gear
- 1 ea: 43 tooth rod gear
- 1 ea: tracker top and bottom
- 1 ea: ULN2003 case and lid
- 1 ea: Raspberry Pi cases

Also included are 3D prints to test hardware and gears.  Use them!

### TEST models

- File: [tracker.scad](../src/scad/tracker.scad)
- Parts: **TEST: Hardware**, **TEST: Gears**
- STL: [TEST-hardware.stl](../src/stl/TEST-hardware.stl), [TEST-gears.stl](../src/stl/TEST-gears.stl)

This contains two test.  One is a block that you can test the bearing and **all** threaded hardware.  The other you verify placement of gears.  The gear placement model is techincally optional but I liked testing the gears on a quick print (30 minutes) before firing up the full tracker print (15 housr).

Please use these before you print the full model!  This will let you know if you need to tune any parameters for final print, including gear placement.

The "TEST: Hardware" model is very busy.  What you're testing and the params to tweak:
- Bearing = try pressing your bearing into the model.  It's better to break the test than the real model!
    - `bearing_diameter`
    - `bearing_height`
- EZ-Finder Mount = if you have a finder, see if it fits on here
    - nothing to tweak, it's hard coded.. you can glue something to the flat surface
- Visual Finder = just for reference, you don't do anything with this but look through without aid
    - nothing to tweak
- Camera Bolt = test your camera bolt goes into this as desired
    - `camera_bolt_diameter`
- Tripod = verify tripod bolt fits
    - `tripod_bolt_diameter`
- Hinge Bolt = test the hinge bolt
    - `hinge_bolt_diameter`
- Rod, Top = make sure the rod fits as desired
    - `rod_diameter`
- Rod, Bottom = the curve should be OK for the model, but you can verify with this
    - `rod_diameter`
    - `rod_T`

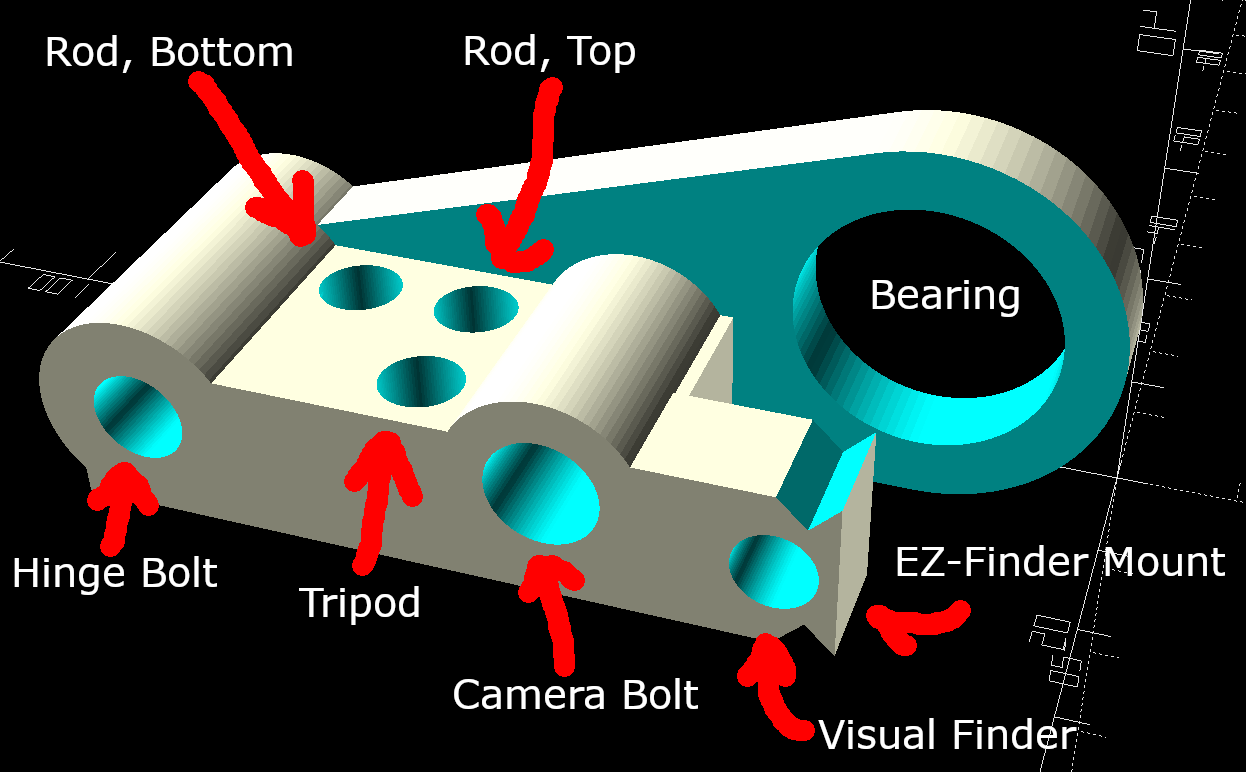
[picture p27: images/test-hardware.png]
TEST Hardware


### GEAR: Stepper

- File: [tracker.scad](../src/scad/tracker.scad)
- Part: **GEAR: Stepper**
- STL: [gear-stepper.stl](../src/stl/gear-stepper.stl)

Only thing you might tweak is the set screw diameter.  I do recommend a set screw as the shaft doesn't have any threads to bite into the stepper gear.  The set screw will ensure alignment of the gear is consistent.  And if you can, put in 2 set screws.  The ones I got were sold in a pack of 2.

- `gear10_set_screw_diameter` = diameter of your set screw hole

### GEAR: Rod

- File: [tracker.scad](../src/scad/tracker.scad)
- Part: **GEAR: Rod**
- STL: [gear-rod.stl](../src/stl/gear-rod.stl)

The defaults get you a 43 tooth gear that fits a 1/4" rod.  I suggest only changing the dimensions for the nut.  You can play around with other factors but make sure you read up on terms!  I used this for reference [Gear Nomenclature](https://en.wikiversity.org/wiki/Gears#/media/File:Gearnomenclature.jpg).

- `gear43_nut_width` = width of the nut
- `gear43_nut_height` = height of the nut

### TRACKER Top and Bottom

- File: [tracker.scad](../src/scad/tracker.scad)
- - Parts: **Tracker Top**, **Tracker Bottom**
STL: [tracker-top.stl](../src/stl/tracker-top.stl), [tracker-bottom.stl](../src/stl/tracker-bottom.stl)

The important bits are the size of your print bed.  I assume a pretty big print bed, sorry.  Maybe you can provide a PR for splitting it?  I didn't want any weak points.

You need to make sure your bolt will fit through the bearing!  The model does not care...  See the TEST: Hardware section for parameters to tweak.  In addition you may want to adjust the width and length of the tracker.  This can be done with:

- `tracker_radius` = how far away the center of the rod is from the hinge
- `hinge_length` = how wide the hinge is, probably a bit shorter than your bolt length to allow for washers and nut

### ULN2003 Case

- File: [tracker.scad](../src/scad/tracker.scad)
- Parts: **ULN2003: Case**, **ULN2003: Lid**
- STL: [ULN2003-case.stl](../src/stl/ULN2003-case.stl), [ULN2003-lid.stl](../src/stl/ULN2003-lid.stl)

Shouldn't need any editing.  This is a simple case with a lid held by friction.  It has slots in the side for wires.  Mount to the tracker as you want.. glue, velcro, weld, whatever.

### Raspberry Pi Case

Not included.  Print what you like.  Attach to tracker.  Examples:

- [Raspberry Pi Pico Case](https://www.thingiverse.com/thing:4733137)
- [Raspberry Pi 3 (B/B+), Pi 2 B, and Pi 1 B+ case with VESA mounts and more](https://www.thingiverse.com/thing:922740)
- [Raspberry Pi 4B Case](https://www.thingiverse.com/thing:3793664)

## Print Settings

This is up to you.  It depends on your printer, how you can remove supports, etc.  What I did:

- Printer: LulzBot TAZ 5
- Nozzle: 0.5mm (stock is 0.35mm)
- Material: PolyLite PLA, True Black
- Layer Height: 0.38mm
- Infill: 40%
- Slicer: Cura LulzBot Edition, version 3.6.0 
- Supports: Custom

I used the [SUPPORT-bearing.stl](../src/stl/SUPPORT-bearing.stl) to only support the bearing holes.  All other holes print fine for me, verified with the [TEST-hardware.stl](../src/stl/TEST-hardware.stl).

**NOTE** it is much quicker to disable automatic slicing while moving around large parts:
1. Settings -> Configure settings visibility...
1. "General" section
1. Uncheck "Slice automatically"
1. Close

In order to use custom support in Cura:

1. Add [TRACKER-bottom.stl](../src/stl/TRACKER-bottom.stl)
2. Add [SUPPORT-bearing.stl](../src/stl/SUPPORT-bearing.stl)
3. Select the SUPPORT-bearing part
4. On the right, select "Custom" for "Print Setup".
5. On the left, select "Per Model Settings" (must be in "Custom" for this to be enabled)
6. Choose "Mesh Type" of "Print as support"
7. Use "Multiply Object" to add 1 more support
8. Move and scale as needed to fill the bearing areas

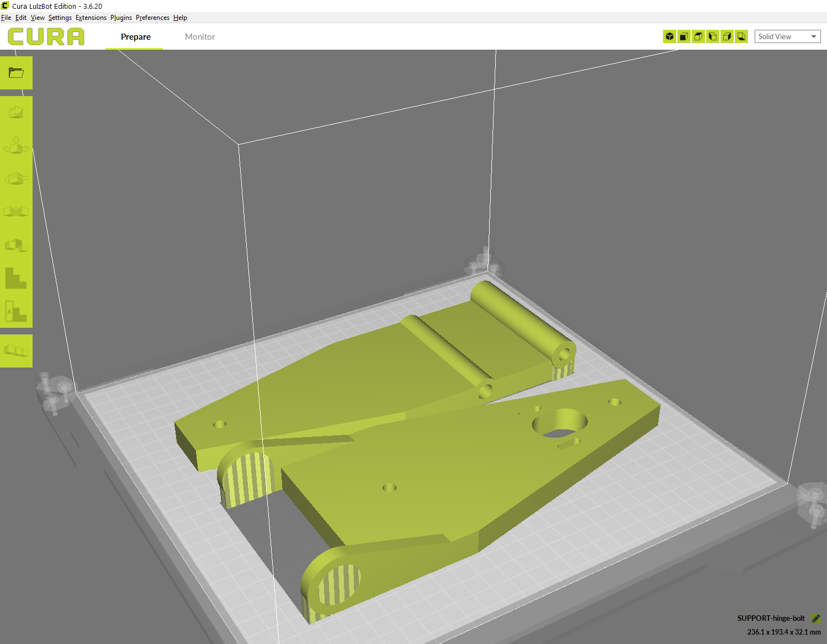
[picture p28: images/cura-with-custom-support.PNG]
Tracker with Custom Support in Cura


## Print Order

I feel it's important to know what to print in what order so you can test and tune for the final product.  See the [TEST models](#TESTmodels) second for tweaking parameters.  I highly **highly** recommend this order.  This is also the order of parts in Customizer..

1. Print "TEST: Hardware".
2. Verify all hardware works.  See [TEST models](#test-models).
3. If adjustments are needed, make adjustments and go back 2 steps.
4. Print "GEAR: Stepper" and "GEAR: Rod".
5. Print "TEST: Gears".
6. Verify gears fit on tester.  See [TEST models](#test-models).
7. If adjustments are needed, make adjustments and go back 2 steps.
9. Print "TRACKER: Top" and "TRACKER: Bottom".
10. [Assemble!](assembly.md)

---
Back to the [Index](00-index.md)!

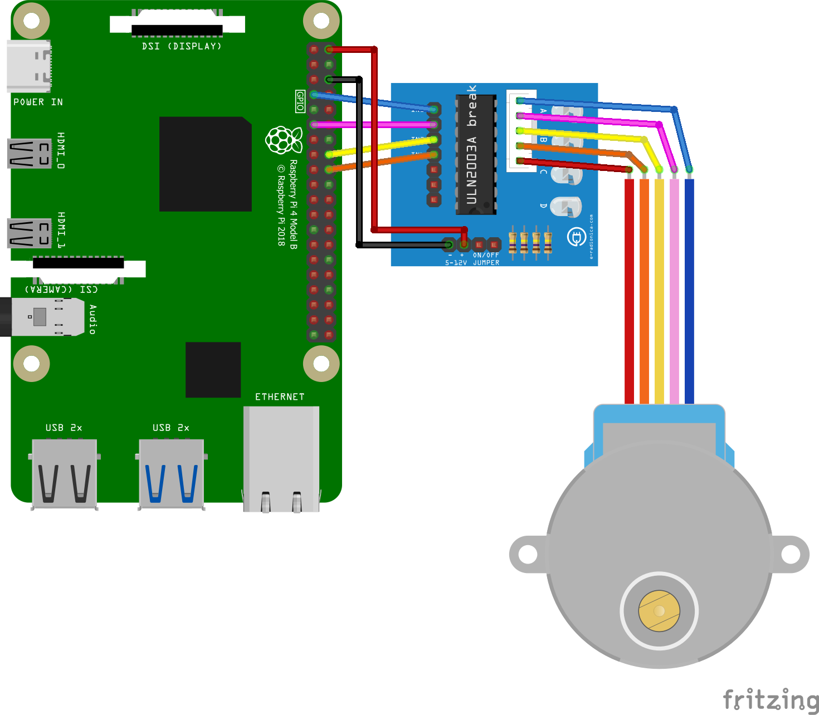
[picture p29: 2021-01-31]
images/wiring-4b.png

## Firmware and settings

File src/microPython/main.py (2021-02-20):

from machine import Pin, Timer
import utime as time
import math
import ujson as json

# this is READ ONLY!
READ_CONFIG_FILENAME="stepper.json"
WRITE_CONFIG_FILENAME="output-stepper.json"
pins_out={}
pins_in={}
config={}

control={
    "forward": 1,
    "locked": True,
    "step_delay_ms": -1,
    "radius": -1,
    "step": 0,
    "timer": {
        "last_start_tick": 0,
        "current_start_tick": 0,
        "counter": 0,
        "expected_ms": 0,
        "actual_ms": 0,
        "last_ms": 0
    },
    "handlers": {
        "step": False,
        "status": False,
        "faster": False,
        "slower": False,
        "forward": False,
        "stop": False
    }
}
timers={}
status_blink_count=0

def load_config():
    config={}
    with open(READ_CONFIG_FILENAME, 'r') as f:
        config=json.loads(f.read())
    return config

def tick():
    # get some tick metric, diff_ms must handle the unit
    return time.ticks_us()

def diff_ms(now,then):
    # see tick() for units
    return time.ticks_diff(now, then) / 1000.0

def startup():
    global pins_out,config,logging_filename

    # initialize output pins
    for key in config['gp_out'].keys():
        value=config['gp_out'][key]
        if key == "startup_gp_on":
            # special case, we handle it later
            continue
        elif isinstance(value,list):
            pins_out[key]=[]
            for g in value:
               pins_out[key].append(Pin(g, Pin.OUT))
        else:
            pins_out[key]=Pin(value, Pin.OUT)

    # turn on the "on startup" outputs
    if 'startup_gp_on' in config['gp_out']:
        for key in config['gp_out']['startup_gp_on']:
            pins_out[key].on()

    # initalize input handlers
    for key in config['gp_in'].keys():
        gpio=config['gp_in'][key]['gpio']
        pin=Pin(gpio, Pin.IN, Pin.PULL_DOWN)
        pins_in[key]=pin

    # initialize input handlers
    # since stop is disabled, forward is also disabled
    #pins_in['forward'].irq(trigger=Pin.IRQ_FALLING, handler=handle_up)
    # turns out it's SUPER annoying to have this stop when tuning speed.. removing for now
    #pins_in['stop'].irq(trigger=Pin.IRQ_FALLING, handler=handle_down)
    pins_in['faster'].irq(trigger=Pin.IRQ_FALLING, handler=handle_left)
    pins_in['slower'].irq(trigger=Pin.IRQ_FALLING, handler=handle_right)
    pins_in['lock'].irq(trigger=Pin.IRQ_FALLING | Pin.IRQ_RISING, handler=handle_center)
    #pins_in['status'].irq(trigger=Pin.IRQ_FALLING, handler=handle_center)

        # INITIALIZE STATE
    # initialize lock
    control['locked']=config['start_locked']
    if not control['locked']:
        pins_out["lock"].on()
    # start with configured radius
    control['radius']=config['tracker']['radius']

    # start the timer
    setup_timer()

def setup_timer():
    configure_step_delay_ms()
    frequency=1000.0/control['step_delay_ms']

    # A Timer is used for triggering a step, but is not used to execute the step!
    # When a timer callback is executed the time in a callback the clock for the next trigger starts after returning.
    # The stepper takes about 250ms to update all 4 coils, therefore if done in the callback we're off by 250ms.
    # Instead, the callback updates a flag to indicate a step _should_ be taken, and this is handled in a hot loop.
    #
    # The callback to trigger a step is "trigger_step()".
    # The execution of a step is "do_step()".
    # The control loop watches for a control flat from trigger_step to then fire do_step.
    #
    # The timer callback is a simple as possible. 
    # See https://docs.micropython.org/en/latest/reference/isr_rules.html 

    # setup timer for steps
    if 'trigger_step' not in timers:
        timers["trigger_step"]=Timer()
    timers["trigger_step"].init(freq=frequency, mode=Timer.PERIODIC, callback=trigger_step)

def configure_step_delay_ms():
    # calculate steps per revolution of the stepper
    stepper_gear_1=float(config['stepper']['gear_ratio'].split(":")[0])
    stepper_gear_2=float(config['stepper']['gear_ratio'].split(":")[1])
    stepper_gear_ratio=stepper_gear_1/stepper_gear_2
    stepper_steps_per_rev=360.0 / config['stepper']['stride_angle'] * stepper_gear_ratio

    # calculate steps per revolution of the trackre
    tracker_radius=float(control['radius'])
    tracker_pitch=float(config['tracker']['pitch'])
    tracker_gear_1=float(config['tracker']['gear_ratio'].split(":")[0])
    tracker_gear_2=float(config['tracker']['gear_ratio'].split(":")[1])
    tracker_gear_ratio=tracker_gear_1/tracker_gear_2
    tracker_steps_per_rev=stepper_steps_per_rev / tracker_gear_ratio

    tracker_circumference=tracker_radius*2*math.pi

    target_mm_per_ms=tracker_circumference/config['sidereal_ms']
    target_steps_per_mm=tracker_steps_per_rev/tracker_pitch
    target_steps_per_ms=target_mm_per_ms*target_steps_per_mm
    ideal_step_delay_ms=1.0/target_steps_per_ms

    if config['debug']:
        print("stepper_steps_per_rev: {}".format(stepper_steps_per_rev))
        print("tracker_steps_per_rev: {}".format(tracker_steps_per_rev))
        print("tracker_circumference: {}".format(tracker_circumference))
        print("target_mm_per_ms: {}".format(target_mm_per_ms))
        print("ideal_step_delay_ms: {}".format(ideal_step_delay_ms))
        print("")

    if control['step_delay_ms']!=ideal_step_delay_ms:
        # it changed, update our control
        control['step_delay_ms']=ideal_step_delay_ms
        # and reset the last_start_tick to remove the last step iteration from totals, as it's now wrong.
        # note this doesn't matter for functionality of the tracker, just for `tick error` printed on shutdown
        control['timer']['last_start_tick']=0

def trigger_step(timer):
    global timer_tick
    timer_tick=tick()
    # capture the time the trigger was fired
    control['timer']['current_start_tick']=tick()
    # tell control loop we need to do a step if 'forward' is enabled
    control['handlers']['step']=control['forward']

def do_step():
    control['handlers']['step']=False

    # very basic, do a step
    sequence_values=config['stepper']['sequence'][control['step']]

    # update stepper coil outputs
    for i in range(0, len(sequence_values)):
        pins_out['stepper'][i].value(sequence_values[i])

    # setup next step
    control["step"]=(control["step"]+1)%len(config['stepper']['sequence'])

def shutdown():
    global config

    # turn off output pins
    for key in pins_out.keys():
        value=pins_out[key]
        if isinstance(value,list):
            for pin in value:
                pin.off()
        else:
            value.off()

    # disable all timers (deinit)
    for key in timers.keys():
        timers[key].deinit()

    # print minimal stats (useful for debugging / sanity checking)
    print_status()

def control_loop():
    global control

    while True:
        # Control loop basically executes a bunch of handlers in order of priority.
        # Each "do_X" function must toggle off the handler if it's appropriate!

        if control['handlers']['stop']:
            do_stop()

        if control['handlers']['step']:
            # do the step
            do_step()
            # collect metadata on status (don't allocate new memory, i.e. arrays)
            then=control['timer']['last_start_tick']
            now=control['timer']['current_start_tick']
            if then > 0 and now > 0:
                control['timer']['counter']+=1
                control['timer']['last_ms']=diff_ms(now,then)
                control['timer']['actual_ms']+=control['timer']['last_ms']
                control['timer']['expected_ms']+=control['step_delay_ms']
            control['timer']['last_start_tick']=now

        if control['handlers']['faster']:
            do_faster()

        if control['handlers']['slower']:
            do_slower()

        if control['handlers']['forward']:
            do_forward()

def led_toggle(timer):
    pins_out["led"].toggle()

# https://micronote.tech/2020/02/Timers-and-Interrupts-with-a-NodeMCU-and-MicroPython/
def debounce(pin):
    prev = None
    for _ in range(32):
        current_value = pin.value()
        if prev != None and prev != current_value:
            return None
        prev = current_value
    return prev

def handle_up(pin):
    if control['locked'] or debounce(pin) is None:
        return
    
    control['handlers']['forward']=True

def do_forward():
    control['handlers']['forward']=False
    control['forward']=1

def handle_down(pin):
    if control['locked'] or debounce(pin) is None:
        return

    control['handlers']['stop']=True

def do_stop():
    control['handlers']['stop']=False
    control['forward']=0
    # reset the tick so we don't get any of the time while stopped
    # and do_step will just pick it up again
    control['timer']['last_start_tick']=0

def handle_left(pin):
    if control['locked'] or debounce(pin) is None:
        return

    control['handlers']['faster']=True

def do_faster():
    control['handlers']['faster']=False

    # increment the radius of the tracker
    control['radius']+=config['controls']['faster_increment']
    # setup the timer for steps, it calculates new delay
    setup_timer()
    # small visual indicator, toggle LED then set a timer to toggle again in 1 second
    if 'led' not in timers:
        timers['led']=Timer()
    pins_out["led"].off()
    timers['led'].init(mode=Timer.ONE_SHOT,period=500,callback=led_toggle)

def handle_right(pin):
    if control['locked'] or debounce(pin) is None:
        return

    control['handlers']['slower']=True

def do_slower():
    control['handlers']['slower']=False

    # decrement the radius of the tracker
    control['radius']-=config['controls']['slower_increment']
    # setup the timer for steps, it calculates new delay
    setup_timer()
    # small visual indicator, toggle LED then set a timer to toggle again in 1 second
    if 'led' not in timers:
        timers['led']=Timer()
    pins_out["led"].off()
    timers['led'].init(mode=Timer.ONE_SHOT,period=500,callback=led_toggle)

def handle_center(pin):
    if debounce(pin) is None:
        return

    # don't do a handler for lock, we need the pin state
    do_lock(pin)

    if not control['locked'] and pin.value()<=0:
        control['handlers']['status']=True

def do_lock(pin):
    # if locked
    #   if button is active
    #       start lock timer
    #   else
    #       cancel lock timer
    if pin.value()>0:
        if 'lock' not in timers:
            timers['lock']=Timer()
        timers['lock'].init(mode=Timer.ONE_SHOT,period=config['controls']['hold_lock_s']*1000,callback=toggle_lock)
    elif 'lock' in timers:
        timers['lock'].deinit()

def toggle_lock(timer):
    global status_blink_count

    control['locked']=not control['locked']
    if control['locked']:
        pins_out["lock"].off()
        
        # hate doing this here but I hate having more functions even more.
        # we are firing a timer in the future to setup a timer for blinking.
        # the initial delay encodes the direction of delta
        # the number of blinks encodes the amount of delta

        # how much off the original radius are we?
        radius_delta=control['radius']-config['tracker']['radius']

        # if the delta is positive we have added to radius, so tracker is faster.
        # if slower, do a long period without blinking (10 sec)
        # if faster, do a short period without blinking (2 sec)
        # if at default, do NO delay and blink 3 times

        blink_delay=0
        blink_count=3
        if radius_delta<0:
            blink_delay=10000
            blink_count=int(abs(radius_delta)/config['controls']['slower_increment'])
        elif radius_delta>0:
            blink_delay=2000
            blink_count=int(abs(radius_delta)/config['controls']['faster_increment'])

        # the lock blink count must be 2x the total blinks since it's a dumb toggle
        status_blink_count=blink_count*2

        if 'blink' not in timers:
            timers['blink']=Timer()
        timers['blink'].init(mode=Timer.ONE_SHOT,period=blink_delay,callback=status_timer)
    else:
        pins_out["lock"].on()

def status_timer(timer):
    global config,status_blink_count

    # if not locked, do nothing. ever.
    if not control['locked']:
        return

    # update our timer to fire periodically and toggle the led.
    if status_blink_count>0:
        timer.init(mode=Timer.PERIODIC,freq=config['controls']['status_blink_hz'],callback=status_blink)

def status_blink(timer):
    global status_blink_count
    pins_out["led"].toggle()
    status_blink_count-=1
    if status_blink_count<=0:
        # all done, shutdown the timer
        timer.deinit()

def print_status():
    timer_actual_ms=control['timer']['actual_ms']
    timer_expected_ms=control['timer']['expected_ms']
    timer_count=control['timer']['counter']
    print("")
    print(control)
    if timer_count>0:
        print("avg_actual_delay_ms: {}".format(timer_actual_ms/timer_count))
    if timer_actual_ms>0:
        err_p=(1.0-timer_expected_ms/timer_actual_ms)*100.0
        print("total_error_p: {}%".format(err_p)) # to 1/1000 of a percent

if __name__ == '__main__':
    # TODO load the initial step delay from configuration
    config=load_config()
    
    try:
        # fire up power, pico's LED, and start timer
        startup()

        # the main control loop, does all the things...
        control_loop()
    except KeyboardInterrupt:
        pass
    except Exception as e:
        # unusual, print the stack by raising it
        raise e
    finally:
        # abort abort! turn off all output and print metrics
        shutdown()

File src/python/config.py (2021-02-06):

import sys, getopt, os.path
import time, datetime
import math
import yaml

# Utility to configure initial values for the stepper code.

DEBUG = False
CONFIG_FILENAME="stepper.yaml"
DEFAULT_CALIBRATION_ITERATIONS=30
SIDEREAL_DAY_IN_MINUTES=86164100/60000.0 # sidereal day in ms converted to minutes: http://www.kylesconverter.com/time/days-(sidereal)-to-milliseconds

def error(msg):
    print("ERROR: {}".format(msg))

def help():
    print("TODO: help text")

def save(config):
    # update history
    if 'calculated_ms' in config['delays']:
        latest=None
        if len(config['history']) > 0:
            latest=config['history'][0]

        # assume structure of history is valid

        # create new history if any delays have changed OR we don't have any history
        create_history=False
        if latest is not None:
            for key in config['delays'].keys():
                h_value=latest[key]
                d_value=config['delays'][key]
                if h_value != d_value:
                    create_history=True
                    break
        else:
            create_history=True

        if create_history:
            new_history={}
            new_history['timestamp']=datetime.datetime.fromtimestamp(time.time()).strftime('%Y-%m-%d %H:%M:%S')
            for key in config['delays'].keys():
                new_history[key]=config['delays'][key]
            config['history'].insert(0, new_history)

    with open(CONFIG_FILENAME, 'w') as outfile:
        yaml.dump(config, outfile, default_flow_style=False)

def load():
    config={}
    if os.path.exists(CONFIG_FILENAME):
        with open(CONFIG_FILENAME, 'r') as infile:
            config=yaml.load(infile, Loader=yaml.FullLoader)

    # initialize requrired child objects and arrays
    objects = ['pins','delays']
    arrays = ['history']

    for obj in objects:
        if obj not in config:
            config[obj]={}
    for arr in arrays:
        if arr not in config:
            config[arr]=[]

    return config

def steps_per_revolution(stepper):
    output=-1
    if str(stepper).upper() == "28BYJ-48":
        motor_stride_angle=5.625 # degrees per step
        motor_gear_ratio=64.0 # 64:1 internal gear ratio (motor to shaft)
        output = 360.0/motor_stride_angle * motor_gear_ratio

    return output

def calculate_step_delay_ms(config):
    global DEBUG

    radius=float(config['radius'])
    pitch=float(config['pitch'])
    stepper=config['stepper']
    gear_ratio=config['gearRatio']

    motor_steps_per_rev=steps_per_revolution(stepper)

    gear_1=float(str(gear_ratio).split(":")[0])
    gear_2=float(str(gear_ratio).split(":")[1])
    external_steps_per_rev=motor_steps_per_rev / (gear_1/gear_2)

    tracker_circumference=radius*2*math.pi

    target_mm_per_minute=tracker_circumference/SIDEREAL_DAY_IN_MINUTES
    target_steps_per_mm=external_steps_per_rev/pitch
    target_steps_per_minute=target_mm_per_minute*target_steps_per_mm
    target_ms_per_step=60000.0/target_steps_per_minute

    if DEBUG:
        print("sidereal_day: {}h {}m {}s".format(math.floor(SIDEREAL_DAY_IN_MINUTES/60.0),math.floor(SIDEREAL_DAY_IN_MINUTES%60.0),math.floor(6000.0*(SIDEREAL_DAY_IN_MINUTES-math.floor(SIDEREAL_DAY_IN_MINUTES))/100)))
        print("external_steps_per_rev: {}".format(external_steps_per_rev))
        print("target_mm_per_minute: {}".format(target_mm_per_minute))
        print("target_steps_per_mm: {}".format(target_steps_per_mm))
        print("target_steps_per_minute: {}".format(target_steps_per_minute))
        print("target_ms_per_step: {}".format(target_ms_per_step))
        print("")

    return target_ms_per_step

def make_config(argv):
    global DEBUG

    config = load()

    try:
        opts, args = getopt.getopt(argv,"hdc:r:p:s:g:",
        ["help","debug","calibrate=","radius=","pitch=",
        "stepper=","gearRatio=","pin_v5=","pin_stepperCoils="])
    except getopt.GetoptError:
        help()
        sys.exit(1)

    calculate=False

    valid_config=True

    for opt, arg in opts:
        if opt == "-h":
            help()
            sys.exit()
        elif opt in ("-d", "--debug"):
            DEBUG = True
        elif opt in ("-c", "--calibrate"):
            config['calibrate']['iterations'] = arg
        elif opt in ("-r", "--radius"):
            if 'radius' not in config or config['radius'] != arg:
                config['radius'] = float(arg)
                calculate=True
        elif opt in ("-p", "--pitch"):
            if 'pitch' not in config or config['pitch'] != arg:
                config['pitch'] = float(arg)
                calculate=True
        elif opt in ("-s", "--stepper"):
            if 'stepper' not in config or config['stepper'] != arg:
                config['stepper'] = arg
                calculate=True
        elif opt in ("-g", "--gearRatio"):
            if 'gearRatio' not in config or config['gearRatio'] != arg:
                if len(arg.split(":")) != 2:
                    error("invalid format for '{}'".format(opt))
                    valid_config=False
                else:
                    config['gearRatio'] = str(arg)
                    calculate=True
        elif opt in ("--pin_v5"):
            config['pins']['v5'] = int(arg)
        elif opt in ("--pin_stepperCoils"):
            config['pins']['stepperCoils'] = []
            for coil in arg.split(","):
                config['pins']['stepperCoils'].append(int(coil))

    # make sure we have all the config
    if 'radius' not in config:
        error("'radius' not set")
        valid_config=False
    if 'pitch' not in config:
        error("'pitch' not set")
        valid_config=False
    if 'stepper' not in config:
        error("'stepper' not set")
        valid_config=False
    if 'gearRatio' not in config:
        error("'gearRatio' not set")
        valid_config=False
    if 'v5' not in config['pins']:
        error("'pin_v5' not set")
        valid_config=False
    if 'stepperCoils' not in config['pins']:
        error("'pin_stepperCoils' not set")
        valid_config=False

    if not valid_config:
        help()
        sys.exit(3)

    if calculate:
        # we have been told something new, calculate from ideal
        config['delays']['calculated_ms']=calculate_step_delay_ms(config)

        # and force a calibration
        calibrate_iterations=DEFAULT_CALIBRATION_ITERATIONS

    # save state    
    save(config)

if __name__ == "__main__":
   make_config(sys.argv[1:])

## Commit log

2021-01-26 Added initial stepper code
2021-01-27 Updated stepper logic to include dynamic calibration
    Helps minimize drift over time.
    [stepper.py]
2021-01-28 Added some models
    [case-uln2003.scad, case-uln2003.stl, gear.scad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]
2021-01-28 Updated gear to not embed nut inside the gear
    Just messes up the print and you end up with less material on top on bottom. Just need the nut to rest on top (or be glued into) the 43 tooth gear.
    [gear-43.stl, gear.scad]
2021-01-28 Starting on the readme
    And when I have the foundation of that done I'll design the model for printing. The wood version I have now isn't so great.
    [tracker.scad]
2021-01-29 Readme and creating tracker.scad
    Bulk of the tracker model is done. Need to add a set of test models and remove some material. And add a place to put the stepper!
    [tracker.scad]
2021-01-29 Tracker tweaks and test model
    Stacking all the holes needed into a single test print. I'll document it in the readme later..
    [support-bearing.scad, support-bearing.stl, tracker-test.stl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]
2021-01-29 Reworked gears and added gear testing model
    Include the 10 tooth gear now and merged all models into tracker.scad. README is partially updated, more sections need fleshed out.
    [TESTER-gears.stl, TESTER-hardware.stl, gear-10.stl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]
2021-01-29 Updated gear and set location for motor.
    Starting to work on material reduction.
    [gear-43.stl, tracker.scad]
2021-01-30 Install readme updates, adjustable stepper location.
    [TESTER-gears.stl, gear-43.stl, tracker-bottom.stl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]
2021-01-30 Models updated and fixed.
    Ready for my own print. More readme updates to come as I put it together and get some pix.
    [SUPPORT-hinge-bolt.stl, TESTER-gears.stl, TESTER-hardware.stl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]
2021-01-30 Added simple finder mount
    On the top, added a visual finder (aka tube) and a mount for an ez-finder II. It's not the dove-tail standard telescope mount so probably not going to work with everything..
    [TESTER-finder.stl, tracker-top.stl, tracker.scad]
2021-01-30 Almost there!
    Tweaks to the model as updating the README. Will add assembly pictures soon. And then need to add wiring and python stuff...
    [GEAR-rod.stl, GEAR-stepper.stl, SUPPORT-hinge-bolt.stl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]
2021-01-30 Updates for mis-aligned bearings
    Added "helper" compass to draw the curve for the _inside_ edge of the threaded rod.
    [HELPER-compass.stl, mini-wedge.scad, mini-wedge.stl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]
2021-01-31 Stepper code updated for 200mm
    and various README updates
2021-01-31 Initial wiring readme, calibration updates
2021-01-31 Wiring diagram!
    And re-wired in stepper code to match diagram (fewer crossing wires!)
    [pi4b+uln2003+28byj-48.fzz]
2021-02-01 Fixed stepper timing
    Wow, it was WAY off.
    [stepper.py]
2021-02-01 Small tweaks
    Added picture of final assembly.
2021-02-01 Added initial wiring for pico
    It may change, I won't get one to play with until later this week..
    [piPico+uln2003+28byj-48.fzz]
2021-02-05 Reworking stepper code
    Adding params and making calibration have limited iterations. I need consistency in the stepping so I can adjust for long term errors (i.e. 2% error over 4 hours).
    [math.py, stepper.py]
2021-02-06 Pico updates!
    Still fiddling with it, pushing in case I mess it up.
2021-02-06 More pico updates
    Docs and code for wiring updates. Better docs on why a pico and what it does.
    [F-wire-blank.scad, F-wire-blank.stl, piPico+uln2003+28byj-48.fzz]
2021-02-07 Using config fully now instead of constants
    except for the initial stepper delay.. need to calculate that then calibrate from it.
2021-02-07 adding a 5-way switch to control the pico
    [5-way-navigation-switch-case.scad, piPico+uln2003+28byj-48+5waySwitch.fzz]
2021-02-07 Slightly slower reverse
    It is causing issues. I may just re-purpose this button. Reverse isn't that fast :D
2021-02-12 Total rework to use timers
    Work is in timer.py, will move to main.py when visual status is worked out.
2021-02-12 Update led_blink.py
    Quick POC for LED bllinking for a specific number of times then stopping.
2021-02-16 Rework of pico code
    Using timers and irq for everything. No more wonky calibration.
    [config.py, main.py]
2021-02-20 Small tweaks
    Tweaked radius of tracker.
    Removed input for up and down.
    Updated stepper gear set screw diameter.
    [GEAR-stepper.stl, tracker.scad]
2021-02-22 Create test-stepper.py
    Script to let me change delay in stepper from the keyboard input.
